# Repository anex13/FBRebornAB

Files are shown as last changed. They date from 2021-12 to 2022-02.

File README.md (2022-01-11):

# Flyingbear Reborn 10mm belt +voron afterburner update

### INTRO

Делюсь своим видиньем перевода 3D принтера FlyingBear Reborn на 10мм ремни и перехода на печатающую голову afterburner от [VORONDESIGN](https://www.vorondesign.com/).

### CONS/PROS

\+ Возможность использовать различные варианты хотенда (V6, Dragon, Dragonfly, Moskito )

\+ Возможность использованиея разрезного ремня (open belt) который дешевле

\+ Двусторонний обдув 4020 турбиной

\+ Обдув радиатора 4010 вентилятором что снижает шум

\+ Возможность установки BlTouch/3DTouch

\+ Более плавная печать за счет 10мм ремней

\+ Легкий и удобный экструдер

\- Небольшое снижение печатающей области

### BOM

##### Для печатной головы Voron Afterburner

M3\*8mm SHCS - 2шт

M3\*12mm SHCS - 2шт

M3\*16mm SHCS - 4шт

M3\*20mm SHCS - 5шт

M3\*30mm SHCS - 6шт

M3\*40mm SHCS - 2шт

[Insert M3D5L4](https://aliexpress.ru/item/4000232858343.html) -12шт

(Все метизы для головы можно [купить набором к примеру тут](https://aliexpress.ru/item/1005003096841891.html) )

[4010 fan](https://aliexpress.ru/item/32727867521.html)

[4020 turbine](https://aliexpress.ru/item/32814937229.html)

[DDB kit](https://aliexpress.ru/item/4000021186440.html) к сожалению пока магазин triangle lab не работает я не могу порекомендовать другие наборы. Можете clockwork заменить на galileo фидер и купить к нему кит.

[v6 не volcano](https://aliexpress.ru/item/32844028127.html)/dragon/moskito honend в сборе в зависимости от выбора

4mm PTFE трубка

[NEMA17 20mm stepper motor](https://aliexpress.ru/item/1005002435137651.html) (ASH для высоких температур до 180С)

[( опционально ) плата разъемов](https://aliexpress.ru/item/1005003559795724.html) ВНИМАНИЕ! в эту плату стоит подключать только куллера охлаждения (только 24в), нагреватель, термистор и мотор. Подключив концевик в разъем probe можно спалить концевик.

##### Для адаптера под FB Reborn

M3\*8mm SHCS - 8шт

M3\*25mm SHCS - 2шт

M3\*10mm SHCS - 2шт

[Insert M3D5L4](https://aliexpress.ru/item/4000232858343.html) -14шт

[Оптический концевик](https://aliexpress.ru/item/32909701232.html) (требуется инверсия относительно стоковых )

(опционально) [ADXL345 aсelerometr](https://aliexpress.ru/item/32949372779.html) для клиппера

(опционально) 3DTouch/BLTouch

(В комплекте крепежа для VORON AB хватает болтов и для адаптера в общем итоге будет необходимо купить комплект и вплавляемые резьбовые втулки)

##### Для перехода на 10мм ремни

[2GT 20 Teeth Synchronou Idler Pulley Bore 5mm](https://www.aliexpress.com/item/32750484488.html) no teeth for belt 10mm - 2шт

[2GT 20 Teeth Synchronou Idler Pulley Bore 5mm](https://www.aliexpress.com/item/32750484488.html) with teeth for belt 10mm - 6шт

[20 teeth GT 2GT 2M Timing Pulley Bore 5mm for belt 10mm](https://www.aliexpress.com/item/32995102911.html) -2шт

[Ремень 2GT open belt 10mm](https://aliexpress.ru/item/902692789.html) \~ 4м ( около 5м если выносить моторы из корпуса )

[Дистанционные шайбы 5х7х0.2 мм](https://aliexpress.ru/item/1005001878385012.html) - пару пакетов по 50шт.

[Болты с плечем m4d5l30 mm](https://aliexpress.ru/item/1005003325718939.html) - 8шт

### MANUAL

#### Печать деталей

##### 1 Voron Afterburner

Скачиваем из официального репозитория <https://github.com/VoronDesign/Voron-Afterburner> STL файлы под необходимую конфигурацию .

(в папке CAD можно найти сборочный чертеж в формате f3d (для Fusion360) и step)

Пояснение:

* В корне папки STLs печатаем все три детали
* В папке Printheads выбираем необходимый хотэнд и печатаем под него обе детали ("printhead_front\*_*имяхотэнда*" и "\*printhead_rear_имяхотэнда" )
* В папке Bowden лежит комплект запчастей под Bowden экструдер если он вам нужен
* В папке Direct_Feed лежит комплект под директ экструдер (Clockwork) на основе экструдера дуал драйв или клона. Из этой папки печатаем [[a]_connector_cover](https://github.com/VoronDesign/Voron-Afterburner/blob/master/STLs/Direct_Feed/%5Ba%5D_connector_cover.stl), [[a]_guidler](https://github.com/VoronDesign/Voron-Afterburner/blob/master/STLs/Direct_Feed/%5Ba%5D_guidler.stl), [[a]_latch](https://github.com/VoronDesign/Voron-Afterburner/blob/master/STLs/Direct_Feed/%5Ba%5D_latch.stl), [[a]_latch_shuttle](https://github.com/VoronDesign/Voron-Afterburner/blob/master/STLs/Direct_Feed/%5Ba%5D_latch_shuttle.stl), [extruder_body](https://github.com/VoronDesign/Voron-Afterburner/blob/master/STLs/Direct_Feed/extruder_body.stl).
* Детали chain_anchor... и [extruder_motor_plate](https://github.com/VoronDesign/Voron-Afterburner/blob/master/STLs/Direct_Feed/extruder_motor_plate.stl) лучше взять из моего архива.
* Все детали с [a] в начале названия можно печатать другим цветом.

##### 2 Печать переходника и усилителей.

В папке STLs 3 папки: Belt idlers supports, VAB adapter, VAB mixed parts

\- Belt idlers supports- тут лежат усилители для роликов балки. Усилители крепятся на 3 болта каждый, и для крепления необходимо дополнительное отверстие для точного сверления которого пригодятся y-max(min) drill conductor которые нужно вставить в отверстия вместо стоковых болтов и просверлить отверстие D3.3mm и нарезать резьбу M4 (можно и просто отверстие пошире чтобы проходила резьба и зажать гайкой ). Один ролик (без зубов на Y-min ) с широким фланцем необходимо обточить чтобы уменьшить один фланец до \~ D15mm (иначе не встанет в балку). Для этого необходимо распечатать 2 детали idler cut support и стянуть этими через эти детали ролик болтом c гайкой м3 вставить эту конструкцию в дрел/шуруповерт и сточить один фланец об напильник/точильный камень (не забудьте пройтись мелкой наждачкой по срезу чтобы убрать всё за что может цепляться ремень).

\- VAB adapter - тут расположен сам адаптер для крепления головы Voron Afterburner . Front и Rear распечатать , при использовании 3D/BLtouch распечатать BLT , вплавить втулки в места подсвеченные на картинках ниже.

\- VAB mixed parts - тут части от головы Voron Afterburner измененные или дополнительные. Если в будущем планируете ставить переходную плату головы вам понадобится MIX pcb spacer и MIX extrudermotorplate for pcb. Так же там лежит MIX zipties *x*chain_anchor для крепления стяжками жгута головы.

##### 3 Порядок сборки

После печати необходимых деталей нужно вплавить резьбовые втулки. На рисунках ниже подсвечены места вплавления втулок именно с той стороны с которой их нужно вплавлять. Места вплавления втулок и сборку самой головы Voron Afterburner можно посмотреть либо в чертеже либо в [официальном мануале по сборке voron 2.4](https://github.com/VoronDesign/Voron-2/blob/Voron2.4/Docs/2.4_Assembly_Manual.pdf) начиная со страницы 66

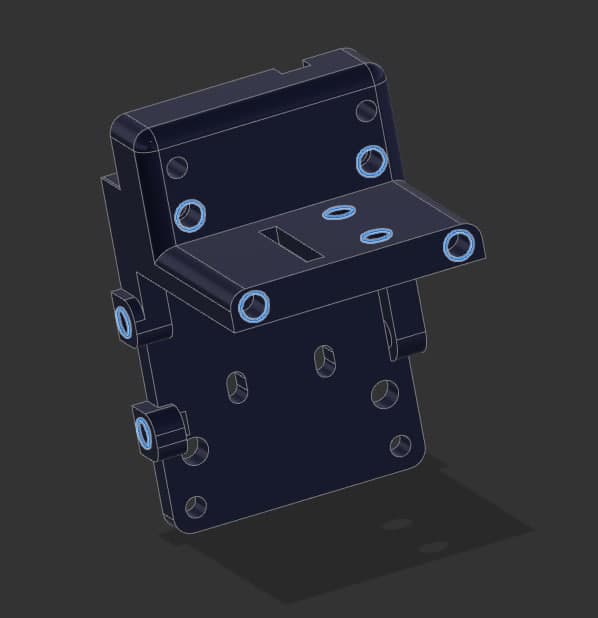
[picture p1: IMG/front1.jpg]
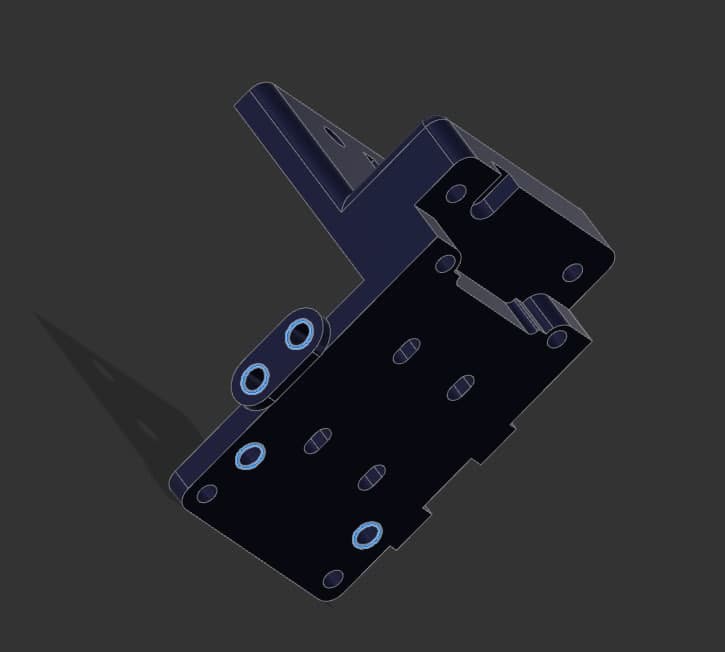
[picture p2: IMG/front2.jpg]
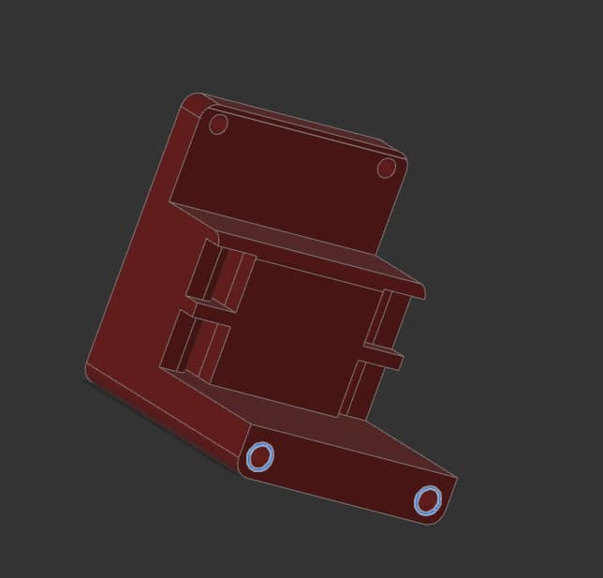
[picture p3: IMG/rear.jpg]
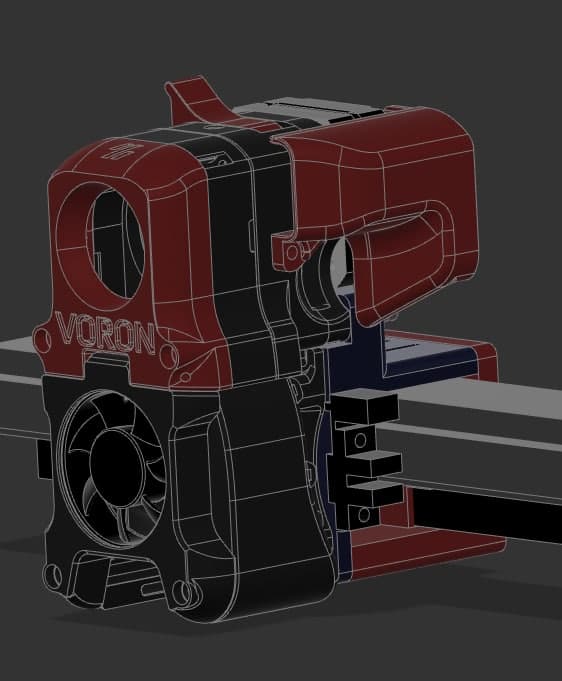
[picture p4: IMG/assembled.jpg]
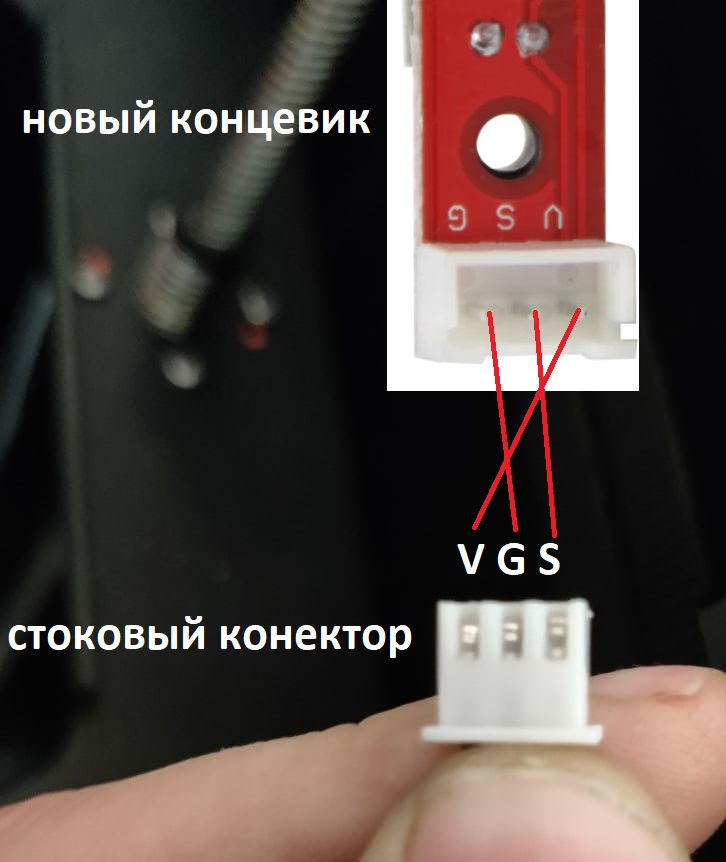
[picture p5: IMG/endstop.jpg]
Подключение концевика


При установке концевика необходимо выпаять разъем и припаять провода напрямую. Также необходимо инвертировать сигнал относительно стоковых .

```
#define Y_MIN_ENDSTOP_INVERTING false
```

Акселерометр крепится сверху над балкой .

При сборке усилителей для роликов , используйте дистанционные шайбы и проверяйте вращение роликов чтобы не перетянуть их.

P.S.

Мне для сборки головы хватило набора крепежа из комплекта и дополнительно пакетика резьбовых втулок. В интернете есть огромное количество модов для этой головы. А еще можно сделать что то самому из исходников.

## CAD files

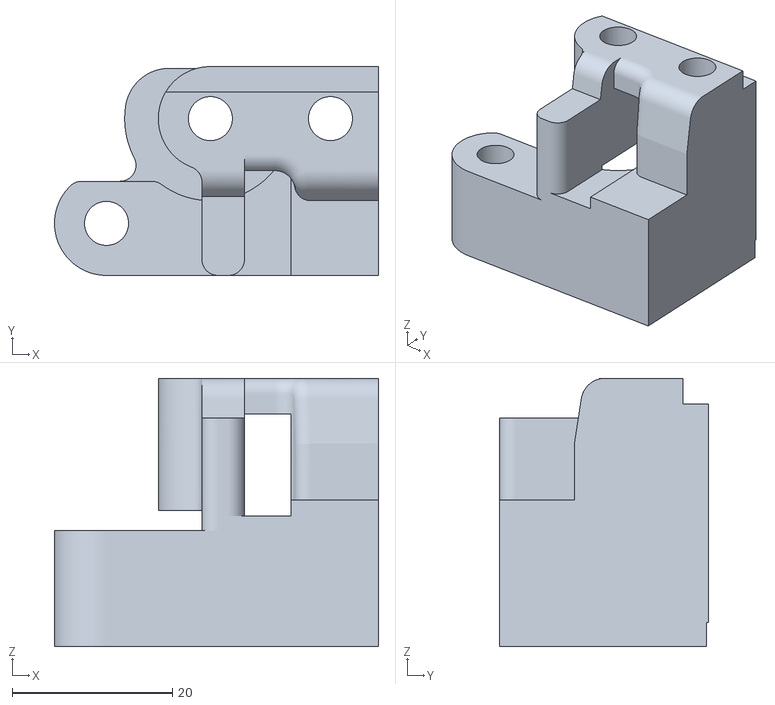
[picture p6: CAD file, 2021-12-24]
STLs/REBORN 10 VAB/Belt idlers supports/y-min.stl
40.5 x 26.1 x 33.5

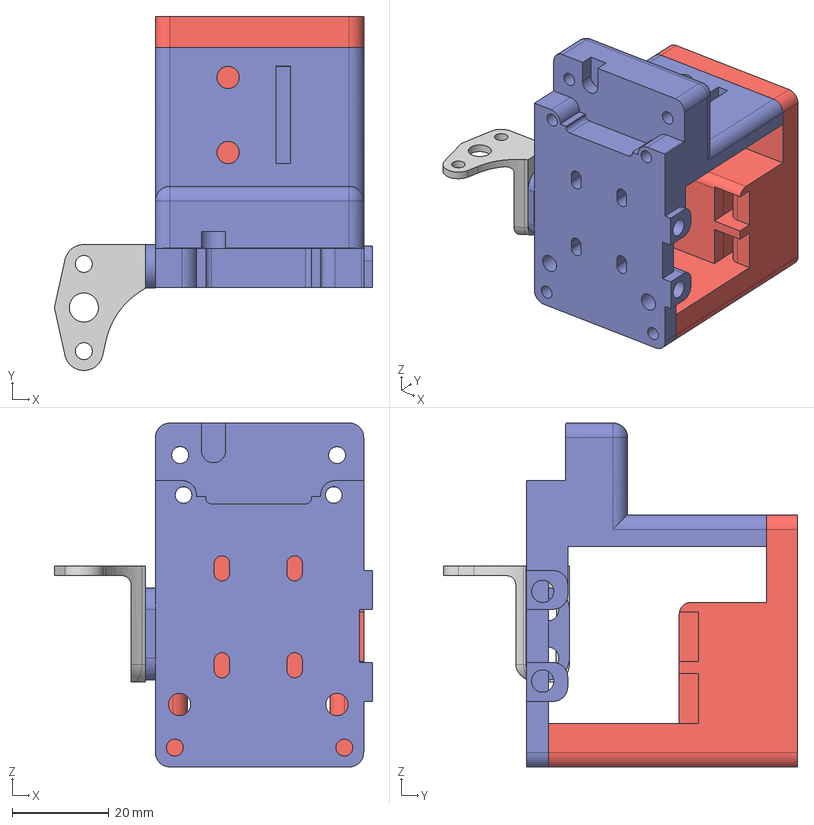
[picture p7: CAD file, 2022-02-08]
STLs/REBORN 10 VAB/VAB adapter/reborn VAB adapter v1.step
65.7 x 73.1 x 71.0 mm

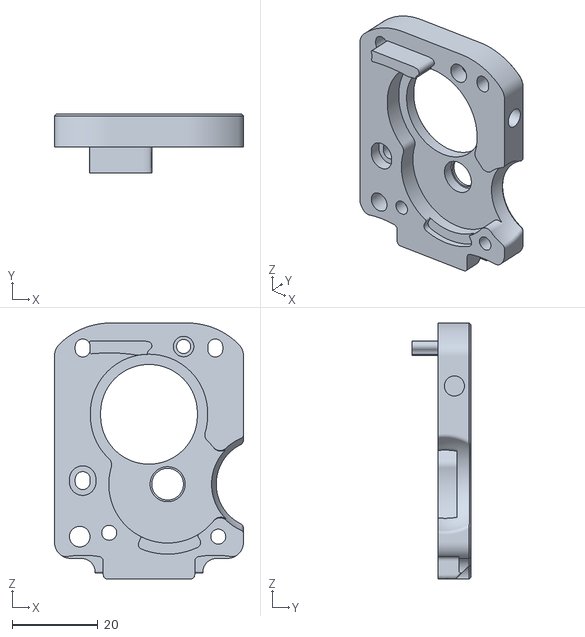
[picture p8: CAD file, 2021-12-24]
STLs/REBORN 10 VAB/VAB mixed parts/MIX extruder_motor_plate for pcb.stl
44.2 x 13.7 x 59.9

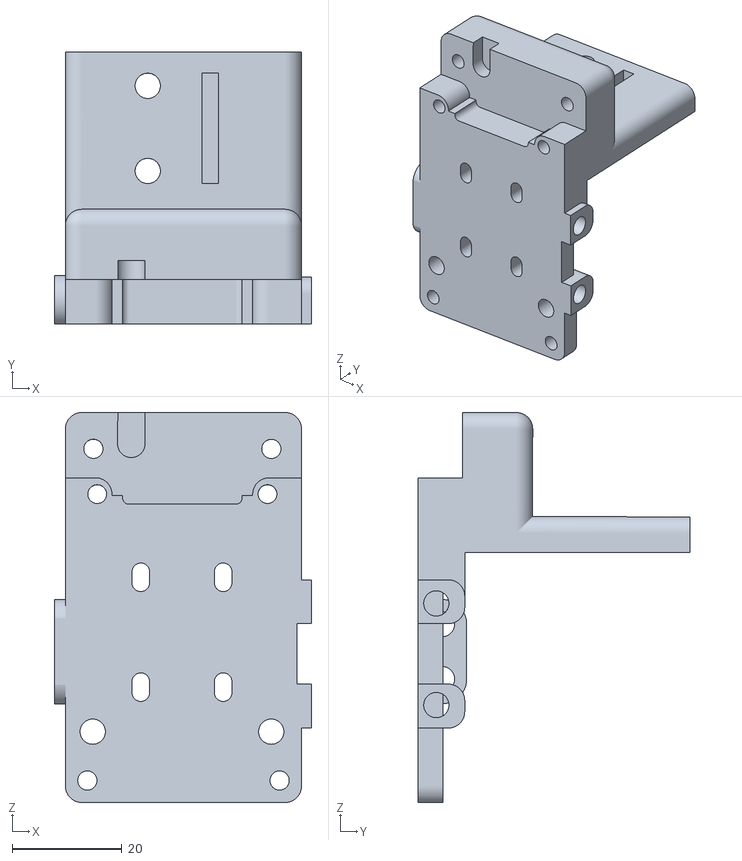
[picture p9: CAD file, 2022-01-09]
STLs/REBORN 10 VAB/VAB adapter/front.stl
46.8 x 49.5 x 71.0

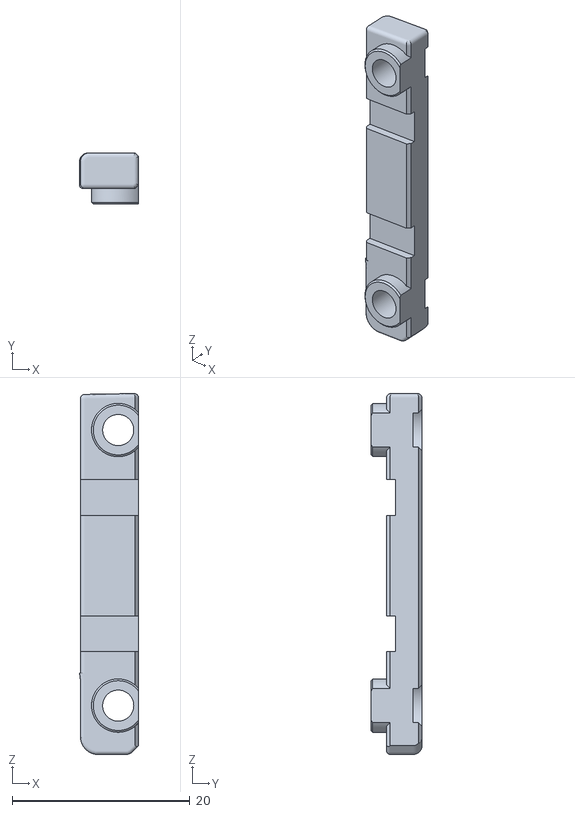
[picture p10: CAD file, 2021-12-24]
STLs/REBORN 10 VAB/VAB mixed parts/MIX zipties_ x_chain_anchor.stl
6.67 x 5.75 x 40.6

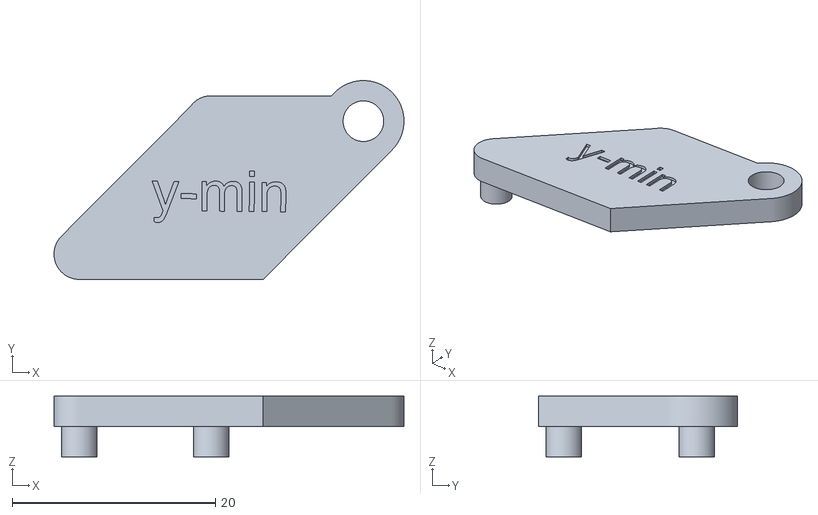
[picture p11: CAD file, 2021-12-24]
STLs/REBORN 10 VAB/Belt idlers supports/y-min drill conductor.stl
34.5 x 19.6 x 6.00

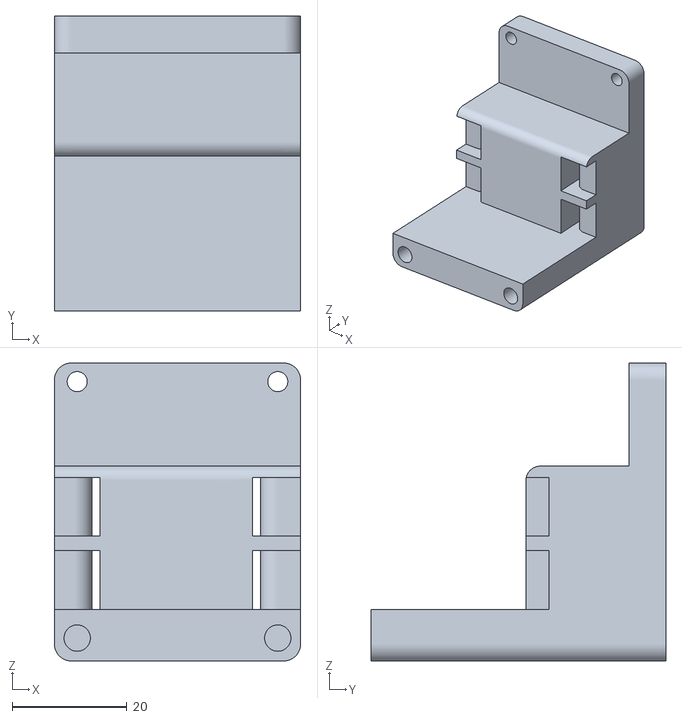
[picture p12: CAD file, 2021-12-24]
STLs/REBORN 10 VAB/VAB adapter/rear.stl
43.0 x 51.4 x 52.0

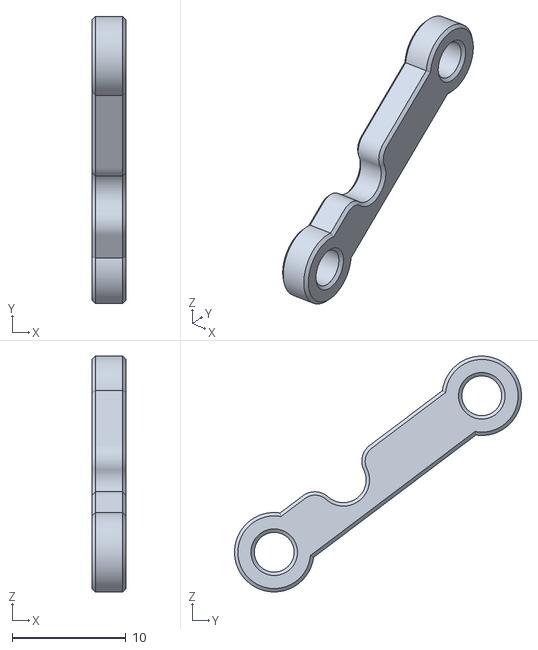
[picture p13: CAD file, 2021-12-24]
STLs/REBORN 10 VAB/VAB mixed parts/MIX pcb spacer.stl
3.00 x 25.3 x 20.8

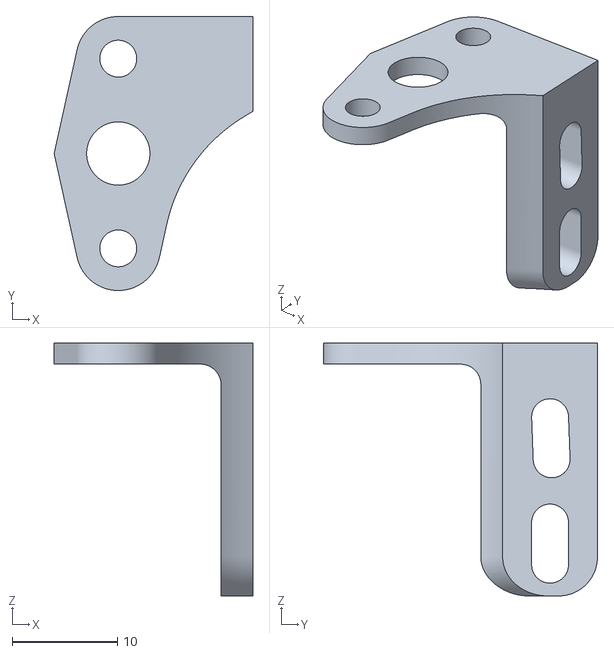
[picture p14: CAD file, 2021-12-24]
STLs/REBORN 10 VAB/VAB adapter/BLT.stl
18.9 x 26.0 x 24.0

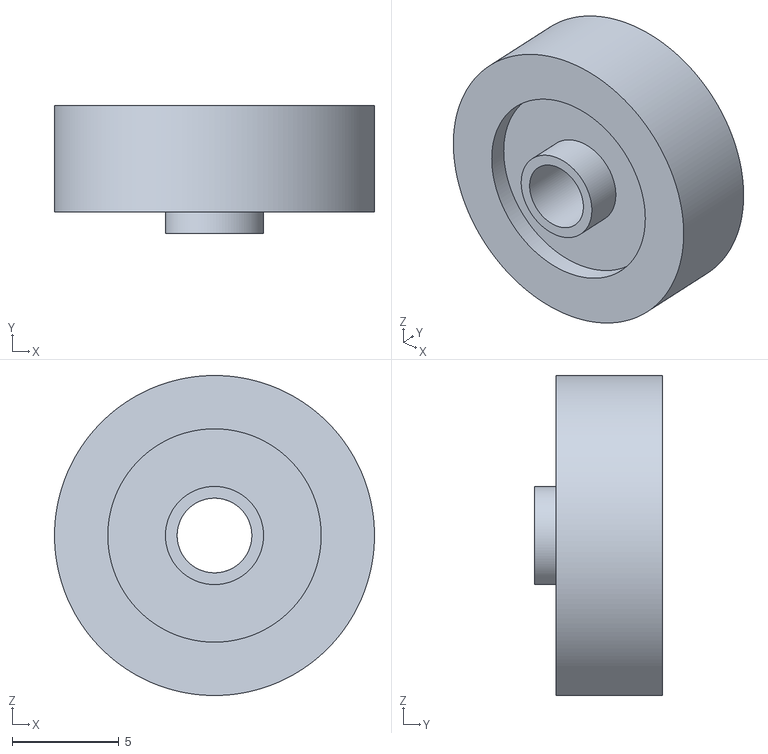
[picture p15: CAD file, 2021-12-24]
STLs/REBORN 10 VAB/Belt idlers supports/idler cut support.stl
15.0 x 6.00 x 15.0

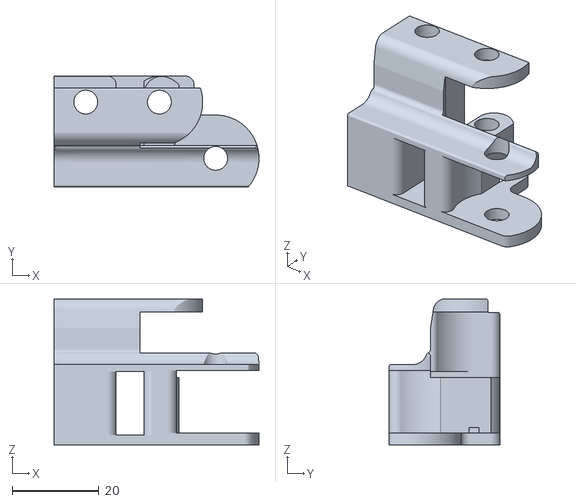
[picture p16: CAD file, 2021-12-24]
STLs/REBORN 10 VAB/Belt idlers supports/y-max.stl
47.3 x 25.6 x 33.7

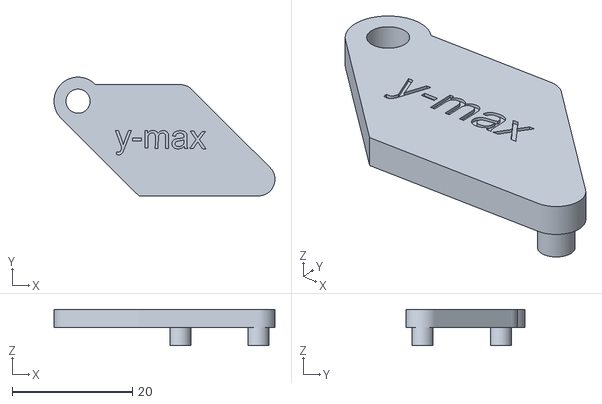
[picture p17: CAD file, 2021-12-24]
STLs/REBORN 10 VAB/Belt idlers supports/y-max drill conductor.stl
36.7 x 19.7 x 6.00

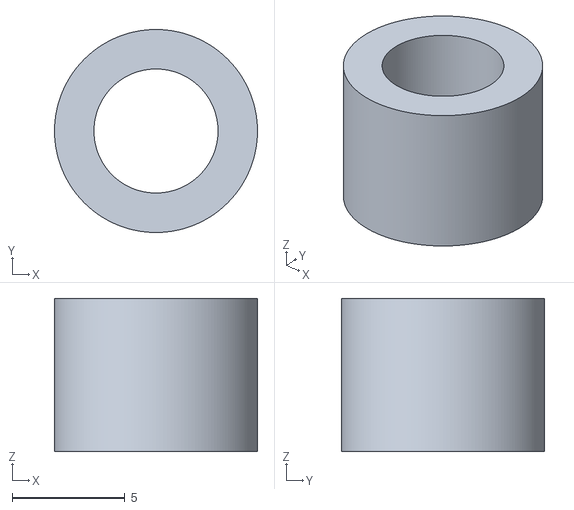
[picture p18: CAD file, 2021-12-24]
STLs/REBORN 10 VAB/Belt idlers supports/68 washer.stl
9.00 x 9.00 x 6.80

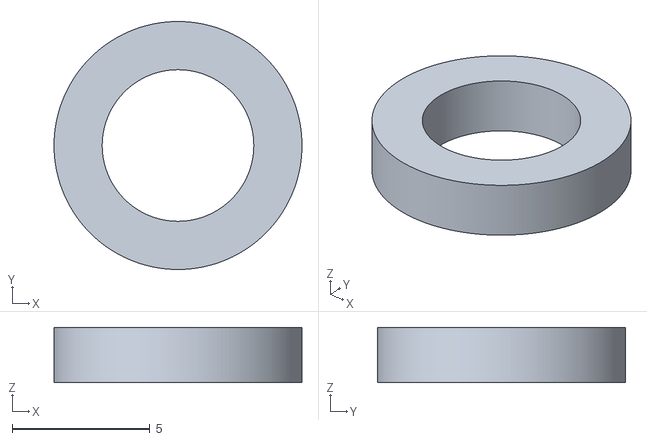
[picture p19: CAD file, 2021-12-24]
STLs/REBORN 10 VAB/Belt idlers supports/20 washer.stl
9.00 x 9.00 x 2.00

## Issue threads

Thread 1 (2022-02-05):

MGN12H

vsoloviev1975, 2022-02-05:
Не могли бы Вы доработать front.stl для каретки mgn12h или выложить исходник, для самостоятельной доработки?
Спасибо!

anex13, 2022-02-08:
Добавил step. под mgn12h там походу придется убрать\перенести крепление bl-touch  в добавок.

Closed 2022-02-08.

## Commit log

2021-12-24 repo added
    [20 washer.stl, 68 washer.stl, BLT.stl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]
2022-01-05 add endstop wiring
    add endstop wiring
2022-02-08 .step file added
    [reborn VAB adapter v1.step]
